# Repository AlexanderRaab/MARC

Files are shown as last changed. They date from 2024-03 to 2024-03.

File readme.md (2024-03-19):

# Project MARC
This repository containes the documentation of the Modular Autonomous Research Companion (MARC).

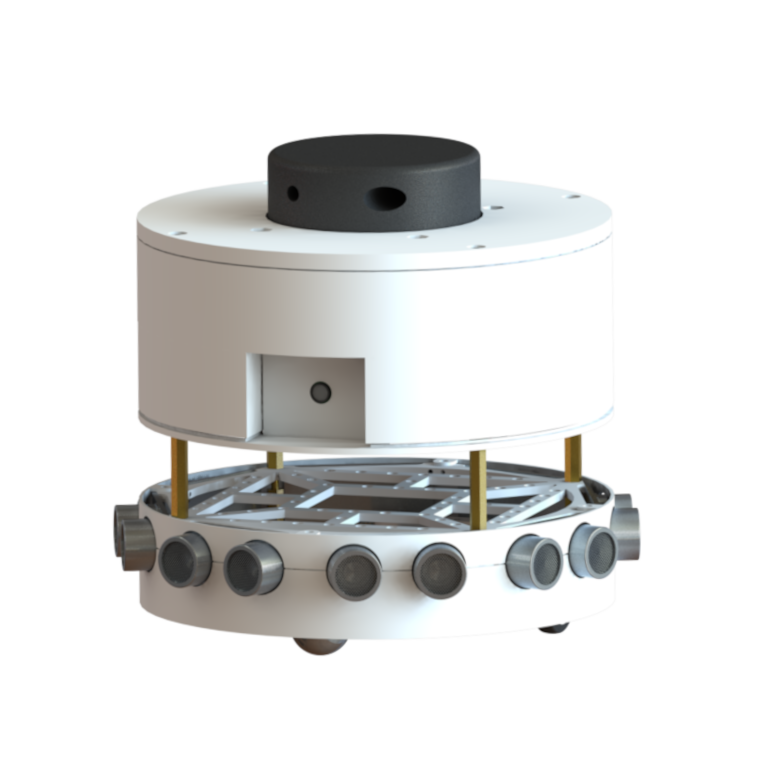
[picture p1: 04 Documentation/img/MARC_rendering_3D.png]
MARC


## Purpose and goal
MARC is a small mobile robot built for at-home testing and experimentation with autonomous robots and all related tasks.
The initial project was started in 2023 with the goal of having a compact and cost-efficient plattform, which can be easily adapted for a multitude of different tasks. For this MARC is setup in different layered modules. Each having a clear functionality as well as providing a defined interface for controlling and for sensory feedback.

## Current status
Up until now, the development mainly focused on setting up the first prototype. Thus, most time was spent on designing a robust implementation of the drive layer, responsible for moving the robot and providing basic sensory feedback for autonomous navigation.

### Hardware
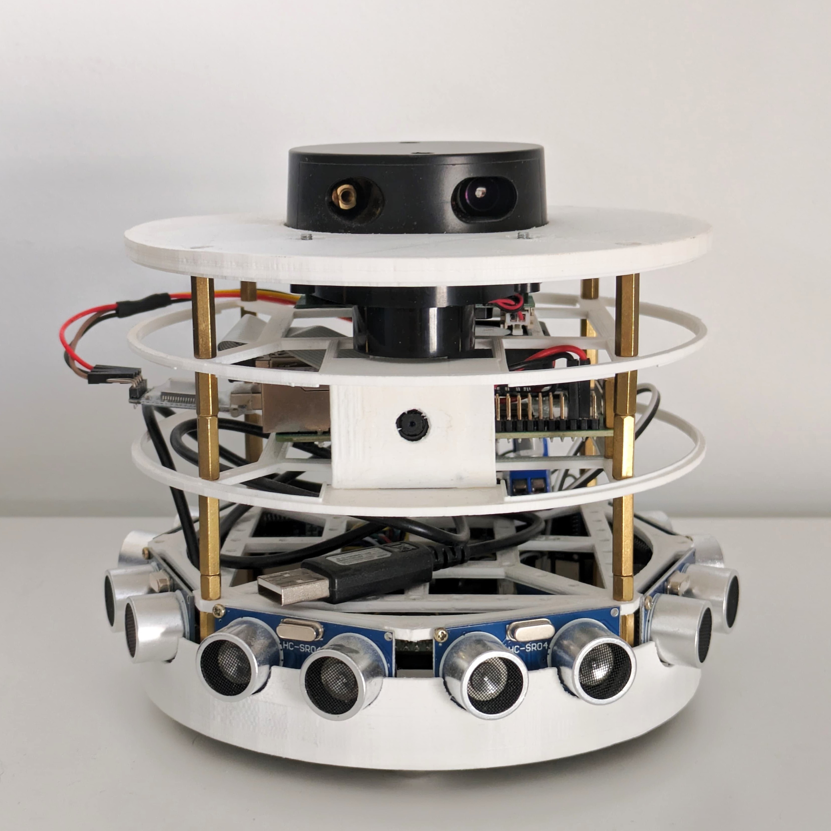
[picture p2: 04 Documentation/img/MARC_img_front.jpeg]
MARC

At this stage, prototypes for the 4 most crucial modules of MARC are completed.

| Module name | Functionality | Interface |
|---|---|---|
| Differential Drive Layer | Locomotion, odometry and basic obstacle detection | micro-ROS via UART |
| Battery Layer | Houses the main battery | n.a. |
| Computation Layer | Containes the main computer and a RGB camera | Joins all other layers |
| LiDAR Layer | Main 2D LiDAR for localization | UART |

#### Differential Drive Layer
This layer is a implementation of a Differential Drive robot. Computations are done on a [Raspberry Pi Pico](https://www.raspberrypi.com/products/raspberry-pi-pico/) mounted on a custom designed PCB. 2 DC motors together with PWM-based motor drivers are used for locomotion. 
The odometry data is currently only computed from wheel encoder signals. Additionally an on-board IMU provides linear acceleration and angular velocity feedback. 
Basic obstacle avoidance can be implemented using 8 ultrasonic distance sensors placed on the circumference of the chassis.

#### Battery Layer
MARC is planned to be powerd either via on-board battery or using a stationary power supply. For now, this layer houses a step-down power supply for converting the input voltage to 12V and 5V in order to supply the other layers.

#### Computation Layer
The main computation unit, a [Raspberry Pi 4B](https://www.raspberrypi.com/products/raspberry-pi-4-model-b/) with 4GB of RAM, is used for all high-level tasks. This includes handling the ROS2 network, processing all data from other layers and providing WIFI connectivity for remote control. Additionally, the main camera is also directly connected to the computer. 

#### LiDAR
For localization, this module contains a 2D LiDAR sensor. The range measurements are streamed over a serial interface and processed directly on the main computer.

### Software
The current version of MARC is based on [ROS2 Humble]( https://docs.ros.org/en/humble/index.html) and [micro-ROS]( https://micro.ros.org/). For now, [Nav2]( https://navigation.ros.org/) is used for all navigation related tasks.

Due to the current focus on hardware prototypes and low-level locomotion control, the ROS2 setup is still under development and may not be completely stable.

Simulation with Gazebo 11          |  Visualization in RVIZ2
:-------------------------:|:-------------------------:
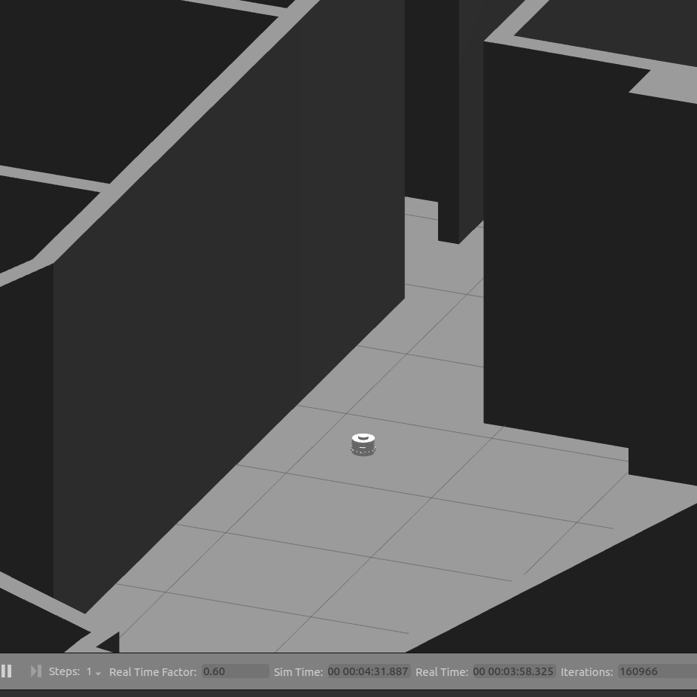
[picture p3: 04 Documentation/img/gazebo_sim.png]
Simulation with Gazebo 11
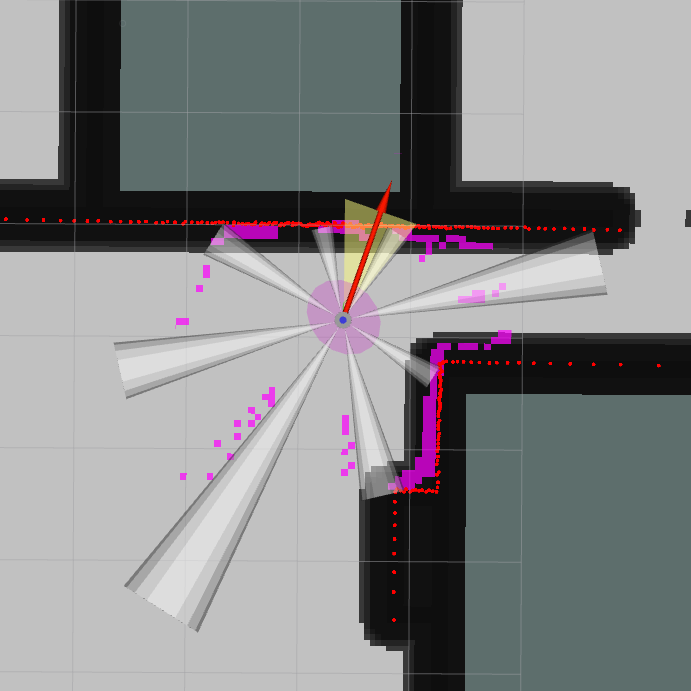
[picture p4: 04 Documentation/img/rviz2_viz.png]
Visualization with RVIZ2
  |  

## Roadmap and planned features

Current development

*   Finishing the intial setup of the ROS2 project for basic SLAM tasks
*   Stabilizing the ROS2 network to improve performance
    *   Revisit the implementation of the camera driver
    *   Improve performance of the custom LiDAR driver
  
Planned features
*   Differential Drive Layer
    *   Implement on-board odometry fusion with an EKF
    *   Change control setup from decoupled PIDs to a model based controller
*   Motion planning and control
    * Implement a trajectory tracking control based on input-output linearization
*   Object detection and classification
    *    Utilize a [YOLO](https://github.com/ultralytics/ultralytics) model for basic on-board detection tasks  
*   Environment interaction
    *   Design and implement a prototype layer for interacting with the environment (e.g. a 3-DOF robotic arm, gripper or fork-lift module)

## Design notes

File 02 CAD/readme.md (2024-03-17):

# CAD
This folder contains all CAD files and assemblies for MARC. Version 1.0 is still in development.

MARC V1.0

## Folder structure
*   Components: 3rd party components for each module
*   Parts: Custom CAD models of individual components
*   Assemblies: Assembled modules
*   Simplified Models: Parts with reduced grade of detail to be used in real-time simulation (includes .stl files)
*   PCBs: Custom PCB files (currently only for the Differential Drive module)

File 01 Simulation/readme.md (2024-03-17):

# Simulation 
This folder contains data and code for simulating parts of the robots software. 

## Data
The _data_ subfolder includes measurement and parameter files for physical components used in the actual robot. Currently only results for the parameter identification of the DC motors can be found there.

## Matlab
Simulations and identification routines can be found in the _Matlab_ folder. 
The following files are currently included:
*   Routines and Matlab code for identifying model parameters of DC motors
    (using an ARX or a 1st order lag element approximation)
*   A SIMULINK model for simulating the Differential Drive kinematics including voltage controlled motors and encoder based odometry

## Example images
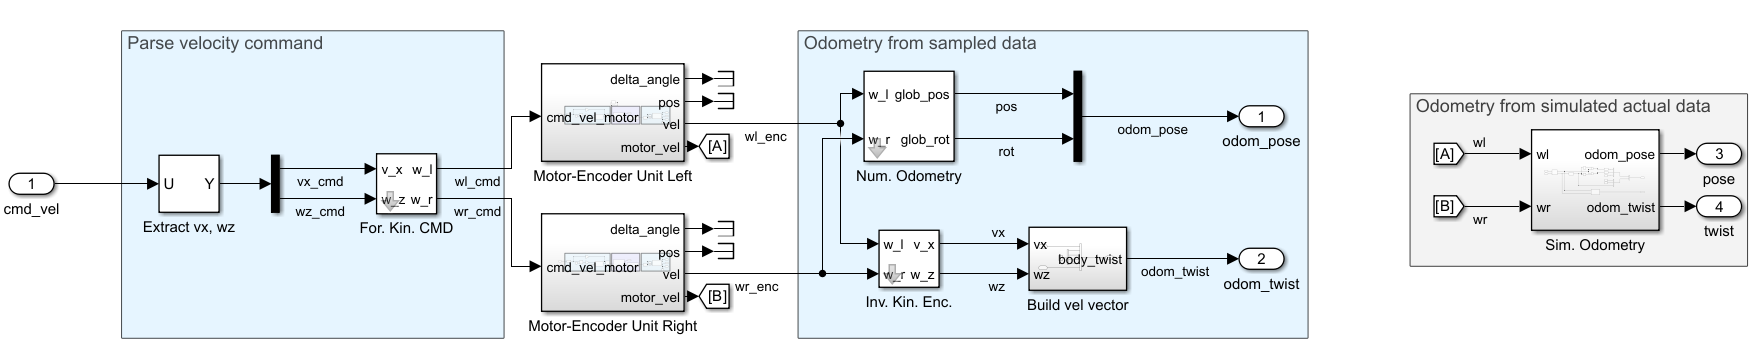
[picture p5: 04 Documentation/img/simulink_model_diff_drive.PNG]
Simulink model


Motor identification ARX model           |  Motor identification PT1 model 
:-------------------------:|:-------------------------:
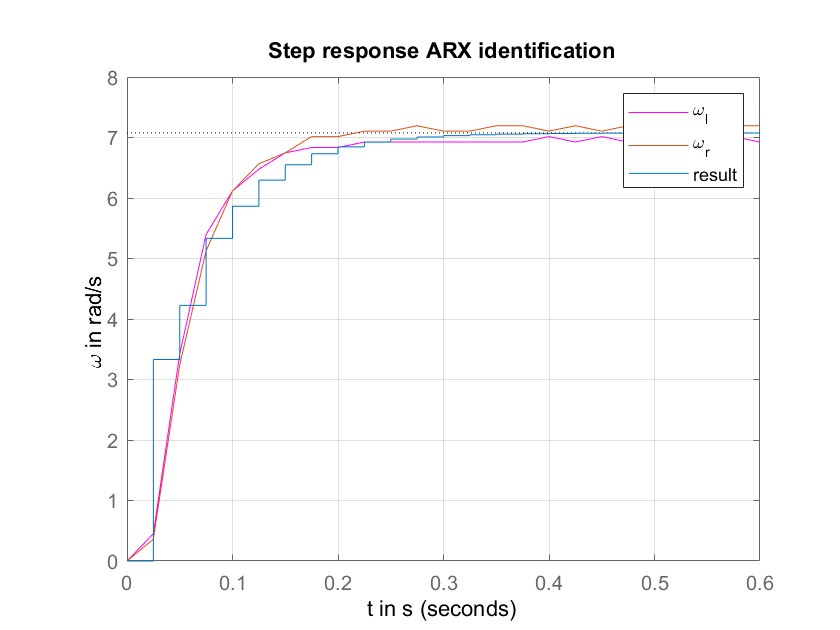
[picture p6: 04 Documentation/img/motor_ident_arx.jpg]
Results ARX identification
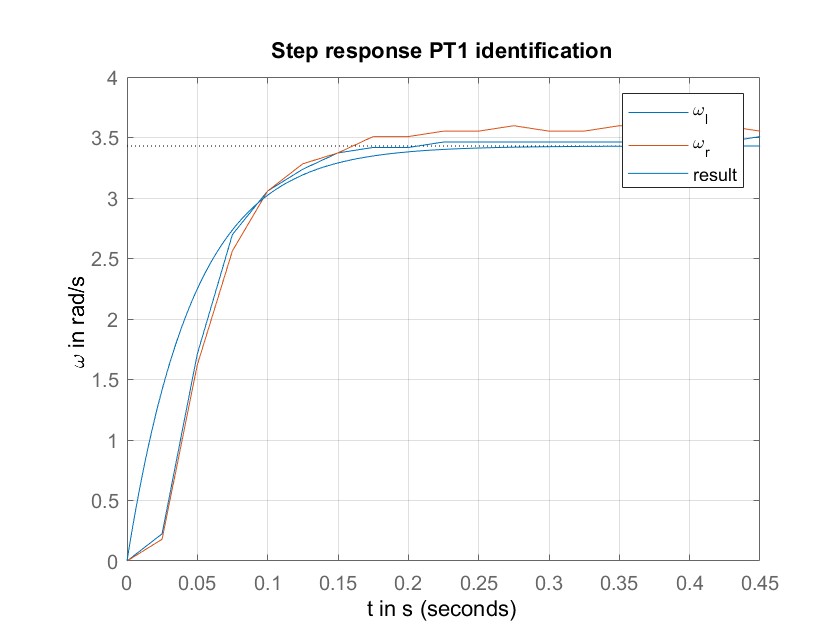
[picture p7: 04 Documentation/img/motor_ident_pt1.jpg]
Results PT1 identification
  |

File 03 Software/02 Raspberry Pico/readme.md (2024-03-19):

# Raspberry Pico
This folder contains code for the Raspberry Pico microcontrollers used to control peripherals of MARC. 

## Pico driver
These directories include the C/C++ code for controlling the Differential Drive module. 

Version 1.0 is only included for completness. Use V1.1, as it includes many stability and performance improvements.

### Setup and tasks
The microcontroller utilizes micro-ROS for integration into the bigger ROS2 project. The implementation is based on timers for executing sampling and control routines. V1.1 fully utilizes both cores of the Raspberry Pico. Core 0 is used for the micro-ROS execution and general sensor sampling including IMU data and ultrasonic range measurements. Core 2 is solely used for kinematic transformations of velocity commands, decoupled DC motor control via PWM and calculation of the wheel odometry.

The implementation is mainly done header-only to stay independet of the hardware platform.

The code project includes the following files:
*   [diff_drive_utils.h](pico_driver_v1.1/diff_drive_utils.h): Methods and calculations Differential Drive kinematics
*   [driver_config.h](pico_driver_v1.1/driver_config.h): Parameter configuration of the driver including dimensions, ROS2 config and control settings
*   [pico_driver.c](pico_driver_v1.1/pico_driver.c): Main project file
*   [pico_interface.h](pico_driver_v1.1/pico_interface.h): Methods for interacting with the Raspberry Pico including reading and writing I/O signals and accessing timers
*   [quadrature_encoder.pio](pico_driver_v1.1/quadrature_encoder.pio): Register-based quadrature encoder reading [source](https://github.com/raspberrypi/pico-examples/blob/master/pio/quadrature_encoder/quadrature_encoder.pio)
*   [ros_interface.h](pico_driver_v1.1/ros_interface.h): Methods for interacting with the ROS2 network e.g. publishing and listening to topics

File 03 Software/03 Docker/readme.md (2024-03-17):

# Docker
This directory includes all files for running the ROS2 project inside a Docker container.

**Attention: The docker environment is still under development and may not work as intended!**
**The implementation is currently only tested for Windows 10 and requires [vcxsrv](https://uni-tuebingen.de/en/fakultaeten/wirtschafts-und-sozialwissenschaftliche-fakultaet/faecher/fachbereich-wirtschaftswissenschaft/wirtschaftswissenschaft/fb-wiwi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)**

## Usage
Paste all custom ROS2 packages to [ros2_ws/src](ros2_ws/src).

On Windows, build the docker container with

    ./build_docker.ps1

Use 

    ./run_docker.ps1

to run the container and

    ./attach_docker.ps1

to open new shell windows.

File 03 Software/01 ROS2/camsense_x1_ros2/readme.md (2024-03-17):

# CAMSENSE_X1_ROS2
This packag is a custom C++ driver and ROS2 wrapper for using the _Camsense X1_ LiDAR.

Credit goes to [Vidicon](https://github.com/Vidicon/camsense-X1) for providing detailed information about the protocol used by the sensor.

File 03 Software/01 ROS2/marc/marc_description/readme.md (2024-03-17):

# MARC_DESRIPTION
This package includes all URDF models of components for MARC.

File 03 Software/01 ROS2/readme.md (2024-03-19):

# ROS2 
This folder contains all custom ROS2 packages. 
**Note: MARC is currently developed for ROS2 Humble**

## Usage
For detailed descriptions of how to run the ROS2 project, check the [marc_bringup](marc/marc_bringup) package.

For launching the default simulation use

    ros2 launch marc_bringup MARC.launch.py simulation:=True

after building an sourcing the workspace.

Use 

    ros2 launch marc_bringup MARC.launch.py simulation:=False

for launching the project on the physical robot.

## Dependencies
The ROS2 project depends on
*   General
    *   [xacro](https://index.ros.org/p/xacro/)  
    *   [rviz2](https://index.ros.org/p/rviz2/)
    *   [robot_localization](https://index.ros.org/p/robot_localization/)
    *   [navigation2](https://navigation.ros.org/)
    *   [robot_state_publisher](https://index.ros.org/p/robot_state_publisher/)
    *   [joint_state_publisher](https://index.ros.org/p/joint_state_publisher/)
*   Simulation only
    *   [gazebo_ros](https://index.ros.org/p/gazebo_ros/)
    *   [gazebo_ros_pkgs](https://index.ros.org/p/gazebo_ros_pkgs/)
*   Physical robot
    *   [micro_ros_agent](https://github.com/micro-ROS/)
    *   [image_tools](https://index.ros.org/p/image_tools/)

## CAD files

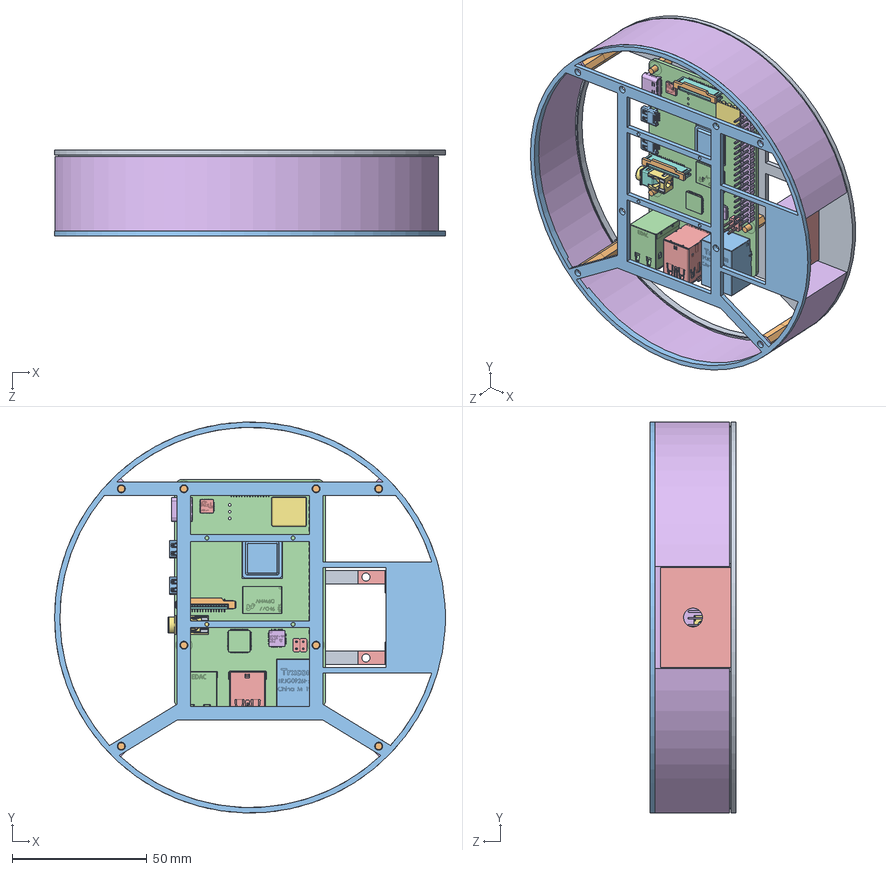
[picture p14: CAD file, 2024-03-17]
02 CAD/V1.0/03 Assemblies/1.02.00 Raspberry Pi 4B Layer.SLDASM
145.0 x 145.0 x 32.0 mm
1.02.01 Raspberry Pi 4B Lower Plate
Spacer M3 x 12
1.02.02 Raspberry Pi 4B Upper Plate
1.0 Plate raspberry Pi 4_1
2.0. PIN HEADER one_1
3.0 PIN HEADER 20_1
4.0 metal plate._1
2.2 part 2 with combine x 2
1.1 part 1 metal pin x 2
3.3 plastic x 2
5.0 CPU Broadcom_1
6.0 9FD77 D9WHV_1
7.0 MxL_1
8.0 Gigabit Ethernet Transceiver_1
9.0 VLI PCIe USB 3.0 Controller_1
card slot part 2 metal pin
sd card slot v1
part 3 v1
11.0 Female micro HDMI connector_1 x 2
15.0 2x USB 2.0 PORT_1
14.0 2x USB 3.0 PORT_1
10.0 Female USB connector_1
part 4 microphone plug
Microphone plug part 1
part 2 microphon plug metal
part 3 microphone plug
12.0 Gigabit ethernet port raspberry
9.0 VLI PCIe USB 3.0 Controller v1_1
1.02.03 Camera Holder
1.02.04 Raspberry Layer Cover

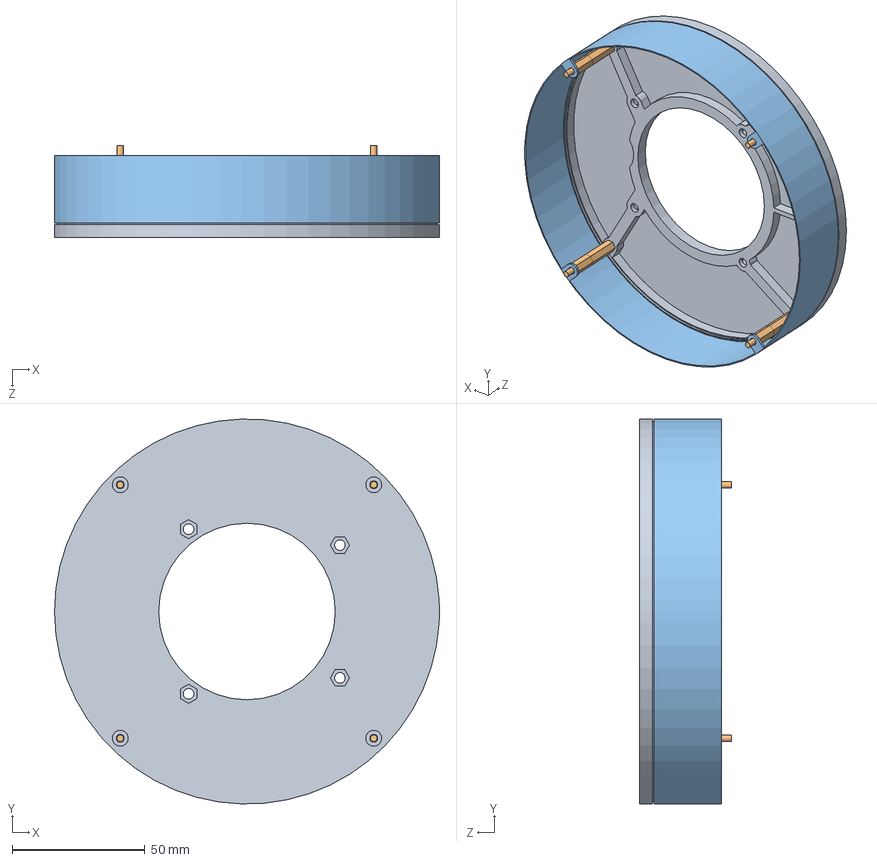
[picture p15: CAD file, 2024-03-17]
02 CAD/V1.0/03 Assemblies/1.03.00 Lidar Layer.SLDASM
145.0 x 144.9 x 34.8 mm
1.03.01 Camsense X1 Plate
Spacer M3 x 8
1.03.02 Camsense X1 Cover

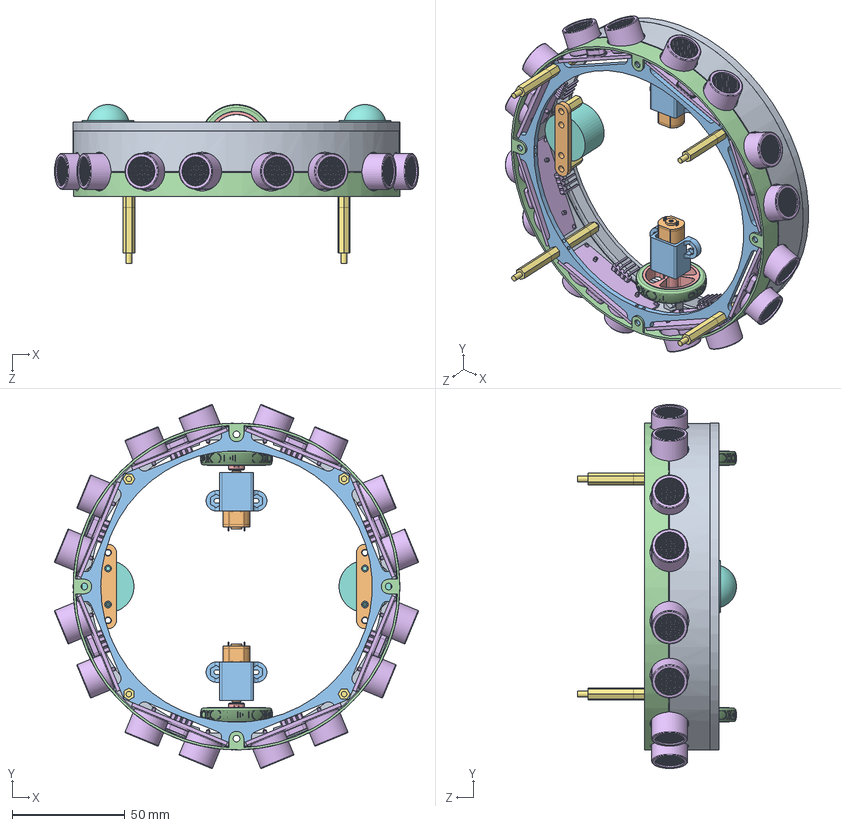
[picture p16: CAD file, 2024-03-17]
02 CAD/V1.0/03 Assemblies/1.01.00 Differential Drive Platform.SLDASM
161.5 x 161.5 x 70.6 mm
1.01.01 Base Layer
Micro Metal Gear Motor x 2
Motor Bracket x 2
Pololu-Wheel-32x7mm-tire x 2
Pololu-Wheel-32x7mm-rim x 2
HC-SR04 x 8
Spacer M3 x 20
Ball Bracer 3_4 x 2
1.01.02 Base Layer Lower Cover
1.01.03 Ball Castor Clip x 2
1.01.04 Ultrasonic Sensor Fixation
1.01.05 Base Layer Upper Cover

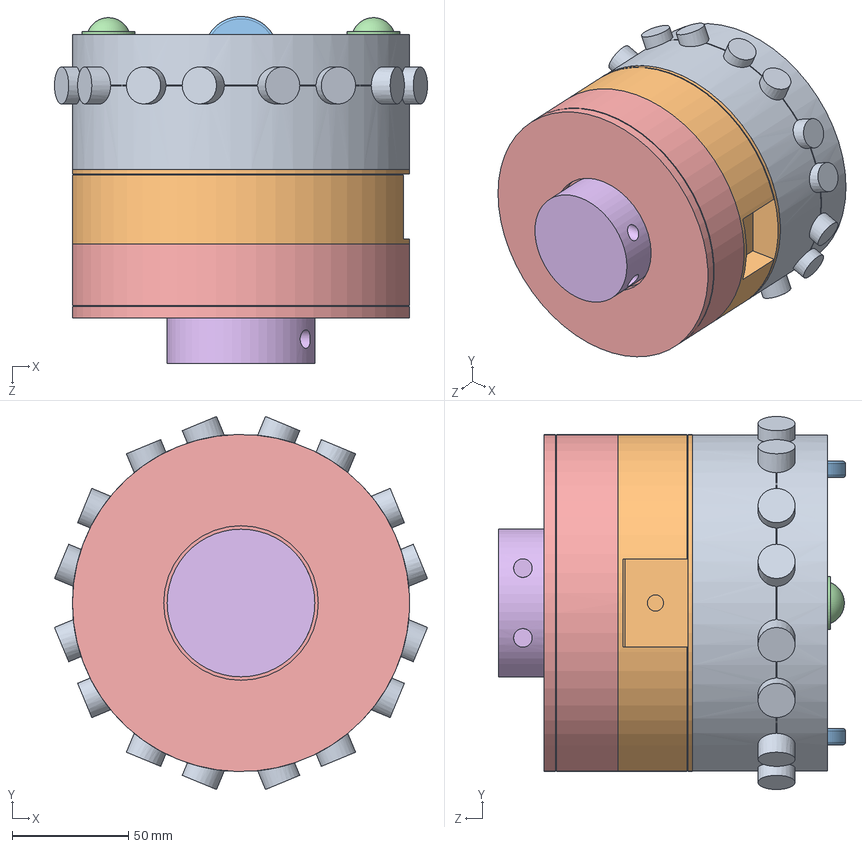
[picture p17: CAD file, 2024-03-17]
02 CAD/V1.0/04 Simplified Models/1.01 MARC Simplified.SLDASM
160.5 x 160.5 x 149.2 mm
1.01 Differntial Drive Plattform Simplified
1.03 Raspberry Pi 4B Layer Simplified
0.01 Wheel 32x7mm x 2
0.02 Ball Castor 075 Inch x 2
1.04 Camsense X1 Layer Simplified
0.03 Camsense X1

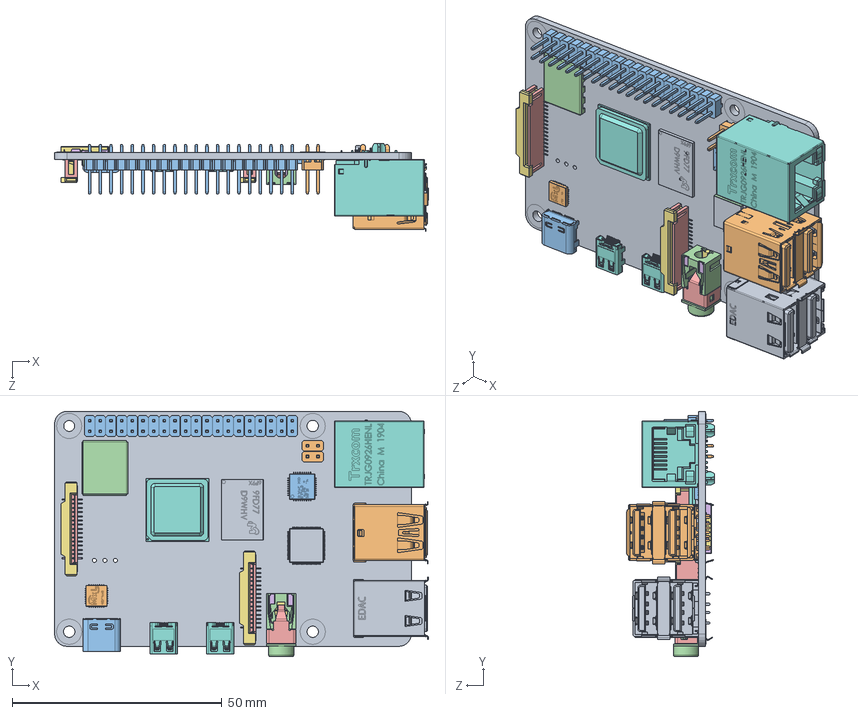
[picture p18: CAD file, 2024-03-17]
02 CAD/V1.0/01 Components/raspberry-pi-4-model-b-5.snapshot.9/Raspberry Pi 4 Model B.SLDASM
89.1 x 58.5 x 20.8 mm
1.0 Plate raspberry Pi 4_1
2.0. PIN HEADER one_1
3.0 PIN HEADER 20_1
4.0 metal plate._1
2.2 part 2 with combine x 2
1.1 part 1 metal pin x 2
3.3 plastic x 2
5.0 CPU Broadcom_1
6.0 9FD77 D9WHV_1
7.0 MxL_1
8.0 Gigabit Ethernet Transceiver_1
9.0 VLI PCIe USB 3.0 Controller_1
card slot part 2 metal pin
sd card slot v1
part 3 v1
11.0 Female micro HDMI connector_1 x 2
15.0 2x USB 2.0 PORT_1
14.0 2x USB 3.0 PORT_1
10.0 Female USB connector_1
part 4 microphone plug
Microphone plug part 1
part 2 microphon plug metal
part 3 microphone plug
12.0 Gigabit ethernet port raspberry
9.0 VLI PCIe USB 3.0 Controller v1_1

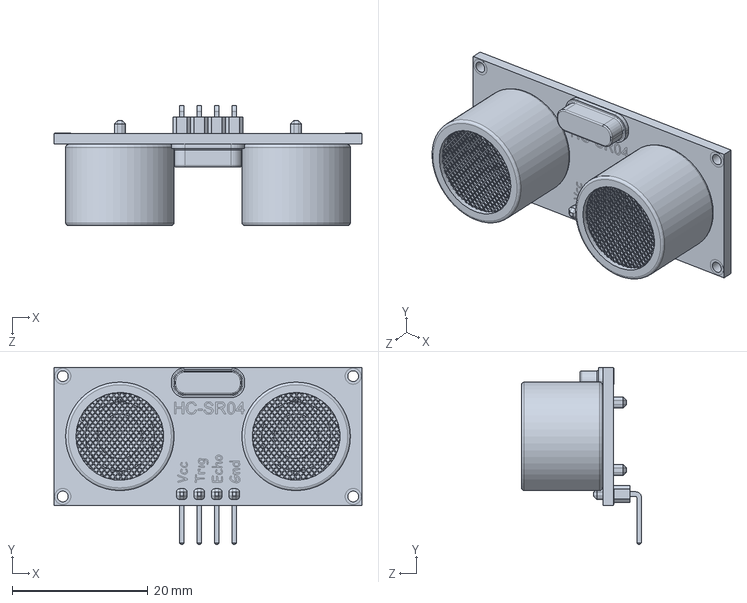
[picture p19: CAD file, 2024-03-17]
02 CAD/V1.0/01 Components/HC-SR04.sldprt
45.4 x 26.1 x 17.7 mm

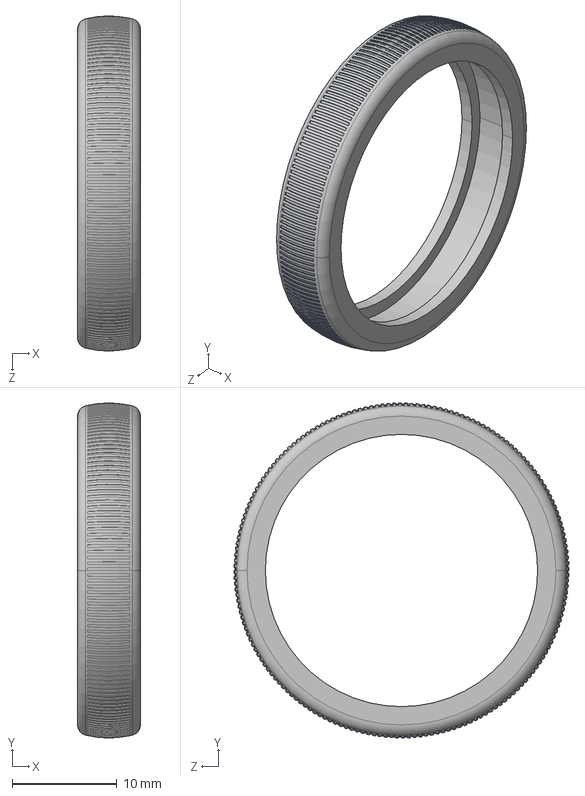
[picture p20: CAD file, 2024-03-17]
02 CAD/V1.0/01 Components/Pololu Wheel 32x7mm/Pololu-Wheel-32x7mm-tire.STEP
6.00 x 32.0 x 32.0 mm

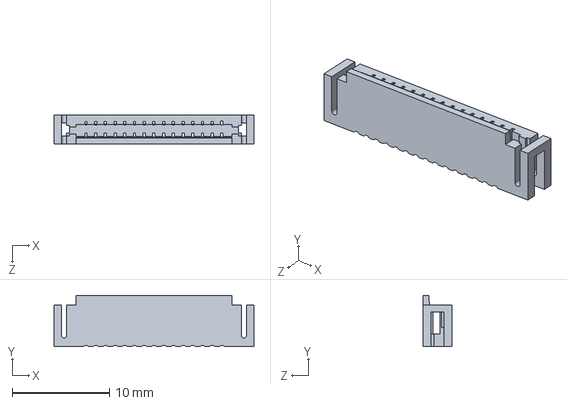
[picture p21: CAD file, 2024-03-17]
02 CAD/V1.0/01 Components/raspberry-pi-4-model-b-5.snapshot.9/1. display connector assembly/2.2 part 2 with combine.SLDPRT
20.6 x 5.30 x 3.00 mm

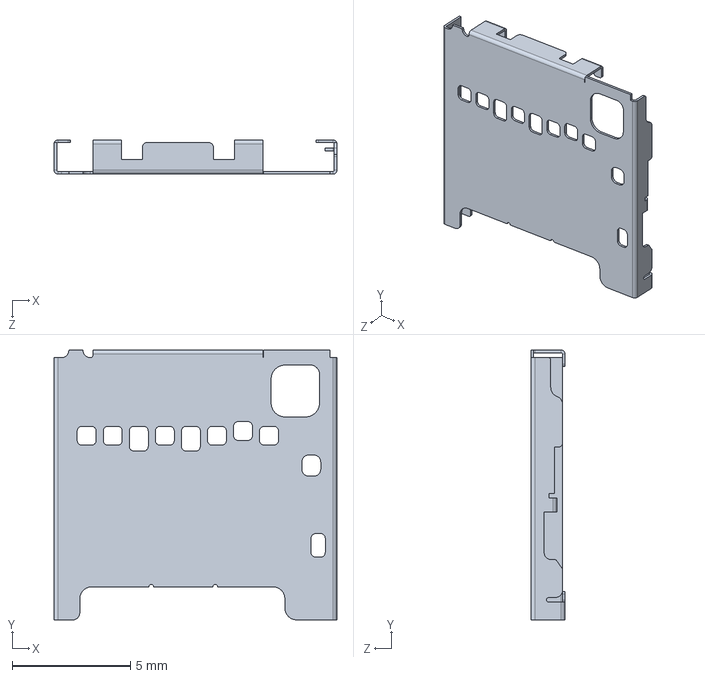
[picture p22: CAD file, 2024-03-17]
02 CAD/V1.0/01 Components/raspberry-pi-4-model-b-5.snapshot.9/2. card slot/part 3 v1.SLDPRT
11.9 x 11.4 x 1.45 mm

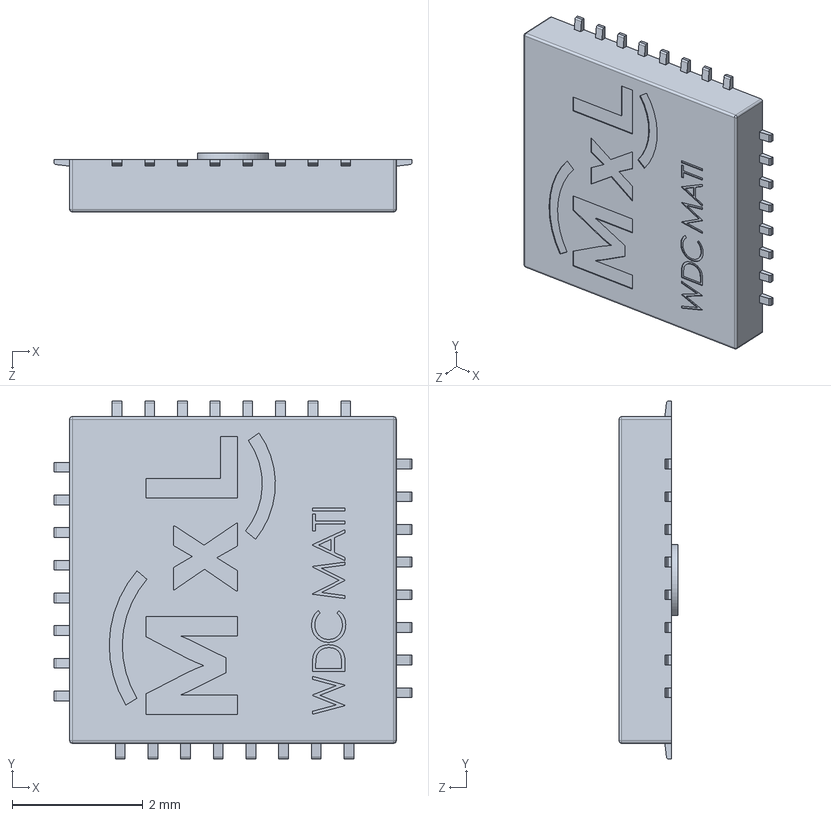
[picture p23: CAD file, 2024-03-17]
02 CAD/V1.0/01 Components/raspberry-pi-4-model-b-5.snapshot.9/7.0 MxL.SLDPRT
5.48 x 5.48 x 0.9 mm

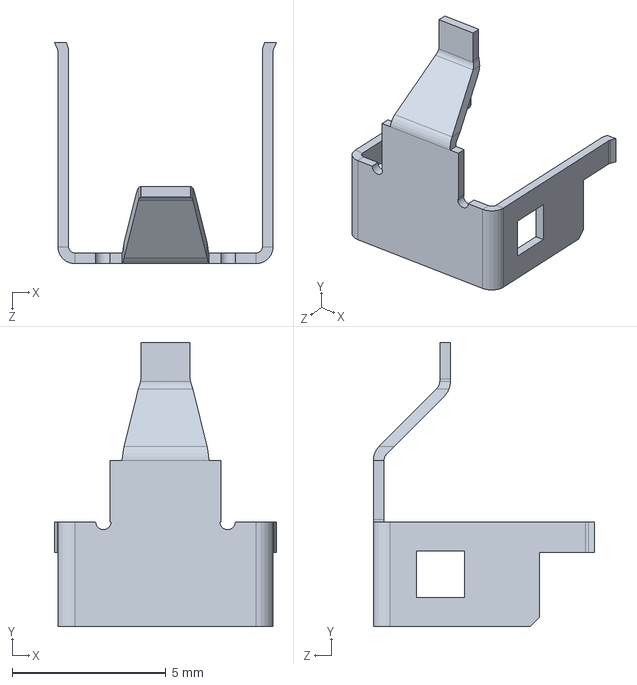
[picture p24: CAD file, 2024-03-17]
02 CAD/V1.0/01 Components/raspberry-pi-4-model-b-5.snapshot.9/Microphone plug/Microphone plug part 1.SLDPRT
7.23 x 9.23 x 7.20 mm

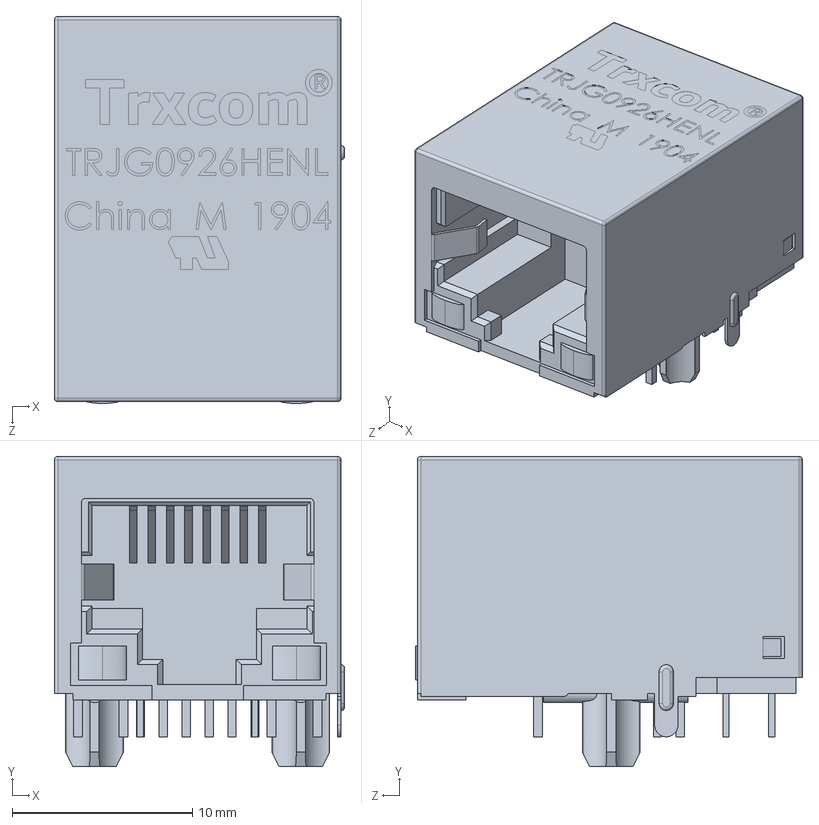
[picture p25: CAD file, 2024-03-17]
02 CAD/V1.0/01 Components/raspberry-pi-4-model-b-5.snapshot.9/Microphone plug/part/12.0 Gigabit ethernet port raspberry.SLDPRT
16.1 x 17.2 x 21.4 mm

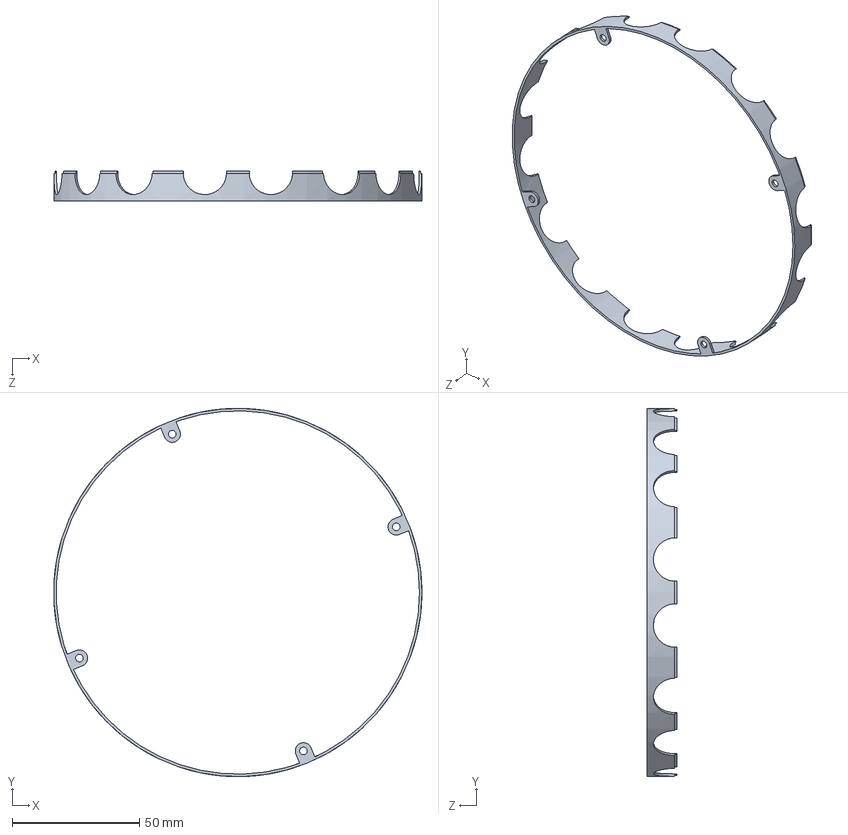
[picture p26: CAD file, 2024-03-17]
02 CAD/V1.0/02 Parts/1.01.05 Base Layer Upper Cover.SLDPRT
144.9 x 144.9 x 11.6 mm

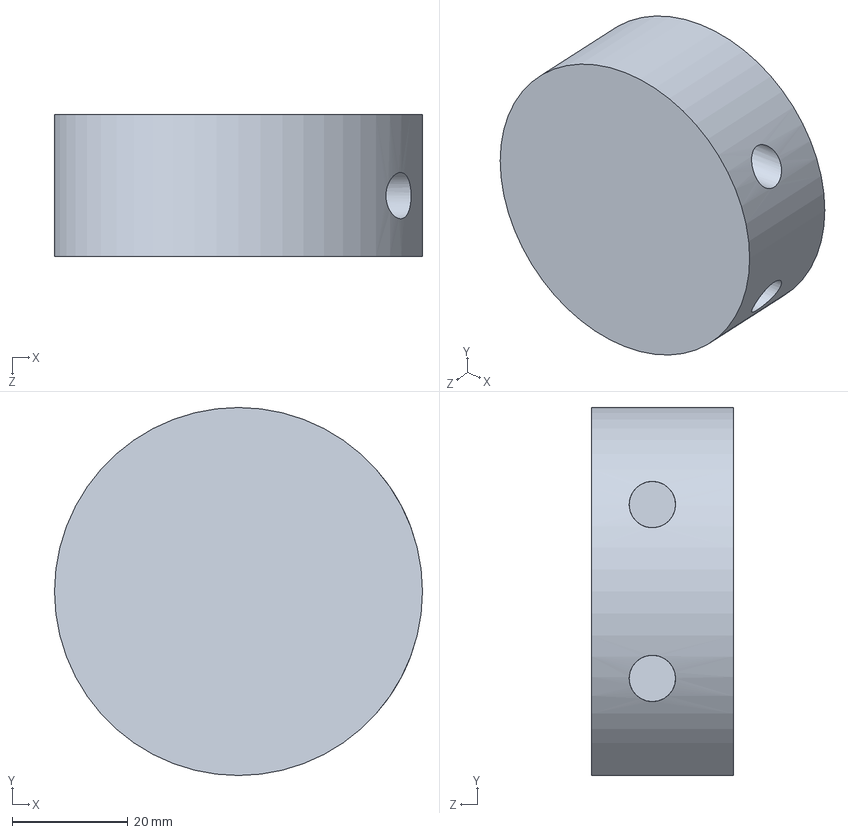
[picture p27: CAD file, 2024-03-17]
02 CAD/V1.0/04 Simplified Models/0.03 Camsense X1.SLDPRT
63.5 x 63.5 x 24.5 mm

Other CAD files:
02 CAD/V1.0/01 Components/raspberry-pi-4-model-b-5.snapshot.9/Display connector assembly_2.sldasm
02 CAD/V1.0/01 Components/raspberry-pi-4-model-b-5.snapshot.9/Display connector assembly.sldasm
02 CAD/V1.0/01 Components/raspberry-pi-4-model-b-5.snapshot.9/Microphone plug assembly.sldasm
02 CAD/V1.0/01 Components/raspberry-pi-4-model-b-5.snapshot.9/Card slot assembly.sldasm
02 CAD/V1.0/01 Components/Ball Bracer 3_4.SLDPRT
02 CAD/V1.0/01 Components/Camsense_X1.SLDPRT
02 CAD/V1.0/01 Components/Camsense_X1_Lidar.SLDPRT
02 CAD/V1.0/01 Components/Micro Metal Gear Motor.SLDPRT
02 CAD/V1.0/01 Components/Motor Bracket.SLDPRT
02 CAD/V1.0/01 Components/Pololu Wheel 32x7mm/Pololu-Wheel-32x7mm - Pololu-Wheel-32x7mm-rim-1.STL
02 CAD/V1.0/01 Components/Pololu Wheel 32x7mm/Pololu-Wheel-32x7mm - Pololu-Wheel-32x7mm-tire-2.STL
02 CAD/V1.0/01 Components/Pololu Wheel 32x7mm/Pololu-Wheel-32x7mm-rim.IGS
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

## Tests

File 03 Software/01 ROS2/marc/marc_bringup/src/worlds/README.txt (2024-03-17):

Gazebo .world file mt_og5.world currently contains absolute path to model file for user "pi" and workspace "dev_ws".
For other user names adjust line 148 and 169 to fit new path.

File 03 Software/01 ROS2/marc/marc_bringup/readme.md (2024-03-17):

# MARC_BRINGUP
This package is used to configure and launch the whole ROS2 project for simulating or running the physical MARC in different configurations.

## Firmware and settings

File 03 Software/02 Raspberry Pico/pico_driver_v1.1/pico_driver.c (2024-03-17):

/* microROS Differantial Driver Robot
    Author:     Alexander Raab
    E-Mail:     alex.raab@liwest.at
    Date:       17.06.2023
    Version:    1.2
    Licence:    TODO

    An application for the Raspberry Pi Pico to work as a ROS2-driver for a differential drive robot.

    TODO: Additional sensors, tf2 publisher odom -> base_link (optional), parameters for relevant variables, 
    optimize for higher sample rates
        
*/


#include <stdio.h>
#include <math.h>

#include <rcl/rcl.h>
#include <rcl/error_handling.h>
#include <rclc/rclc.h>
#include <rclc/executor.h>

#include <rmw_microros/rmw_microros.h>

#include "driver_config.h"
#include "diff_drive_utils.h"
#include "pico_interface.h"
#include "ros_interface.h"

// Shutsdown the node
void shutdown_node()
{
    RCCHECK(rcl_subscription_fini(&cmd_vel_sub, &node_driver));
	RCCHECK(rcl_publisher_fini(&odom_pub, &node_driver));
    RCCHECK(rcl_publisher_fini(&imu_pub, &node_driver));
	RCCHECK(rcl_node_fini(&node_driver));
}

int main()
{
    // Setup transport system for RPi Pico
    rmw_uros_set_custom_transport(
		true,
		NULL,
		pico_serial_transport_open,
		pico_serial_transport_close,
		pico_serial_transport_write,
		pico_serial_transport_read
	);

    // Initilize Pico GPIO etc.
    pico_setup();

    // Initialize controller parameters
    PID_update_parameters(driver.motor_left->velocity_controller);
    PID_update_parameters(driver.motor_right->velocity_controller);

    allocator = rcl_get_default_allocator();

    // Wait for agent successful ping for 2 minutes.
    const int timeout_ms = 1000; 
    const uint8_t attempts = 120;
    RCCHECK(rmw_uros_ping_agent(timeout_ms, attempts));

    // Init support
    rcl_init_options_t init_options = rcl_get_zero_initialized_init_options();
    RCCHECK(rcl_init_options_init(&init_options, allocator));
    RCCHECK(rcl_init_options_set_domain_id(&init_options, DOMAIN_ID));
    RCCHECK(rclc_support_init_with_options(&support, 0, NULL, &init_options, &allocator));

    // Node
    RCCHECK(rclc_node_init_default(&node_driver, "driver_node", NAMESPACE_DRIVER, &support));

    // Setup node functionalities
    setup_publishers();
    setup_subscribers();
    setup_timers();
    setup_msg();

    // Executor
    RCCHECK(rclc_executor_init(&executor, &support.context, CONTEXT_CNT, &allocator));
    RCCHECK(rclc_executor_add_timer(&executor, &timer_sample));
    RCCHECK(rclc_executor_add_subscription(&executor, &cmd_vel_sub, &msg_cmd_vel, &cmd_vel_callback, ON_NEW_DATA));

    // Loop
    gpio_put(PIN_MOT_ON, 1);

    rcl_ret_t ret = RCL_RET_OK; 
    while (ret == RCL_RET_OK)
    {   
        // Perform non-critical tasks 
        if(timer_update_sample)
        {
            update_sonar();
            timer_update_sample = false;
        }
        rclc_executor_spin_some(&executor, RCL_MS_TO_NS(1));
    }
        
    //rclc_executor_spin(&executor);
    gpio_put(PIN_MOT_ON, 0);

    shutdown_node();

    return 0;
}

// Main loop on core 1 - used for velocity control
void core1_main()
{
    repeating_timer_t ctrl_timer;
    add_repeating_timer_ms(TIMER_CONTROL_INTERVAL, timer_ctrl_callback, NULL, &ctrl_timer);

    while(1)
    {   
        if(timer_update_ctrl)
        {

            // Store current velcoity command for use on core 1
            mutex_enter_blocking(&mtx_cmd_vel);
            set_target_vel_body();
            mutex_exit(&mtx_cmd_vel); 

            // Read data from PIO and update measurement data
            mutex_enter_blocking(&mtx_odom_data);
            update_odometry_data(quadrature_encoder_get_count(pio_enc_L, PIO_ENC_L_SM), -quadrature_encoder_get_count(pio_enc_R, PIO_ENC_R_SM));
            mutex_exit(&mtx_odom_data);

            // Apply velocity control
            control_velocity();      
            set_motor_pwm(pwm_out_mot[0], pwm_out_mot[1]);  
             
            timer_update_ctrl = false;
        }
    }

    cancel_repeating_timer(&ctrl_timer);
}

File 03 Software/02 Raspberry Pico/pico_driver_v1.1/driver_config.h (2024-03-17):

/*  Includes all configuration settings for the differential drive plattform.
    Author:     Alexander Raab
    E-Mail:     alex.raab@liwest.at
    Date:       17.06.2023
    Version:    1.1
    Licence:    TODO

    This header is used to store all configuaration settings, global variables and macros relevant for the differential drive plattform in one file.
*/

#pragma once

// ROS2 settings
// --- Main settings
#define DOMAIN_ID (0)
#define NAMESPACE_DRIVER ""                         // Node namespace 
#define NAMESPACE_SENSOR ""                         // Namespace for sensor data

// --- Frames
#define BASE_LINK "base_link"                       // Robot base link
#define IMU_FRAME "imu"                             // IMU sensor link
#define ODOM_FRAME "odom"                           // Odometry link
#define ULTRASONIC_1_FRAME "ultrasonic_1_link"      // Ultrasonic sensor 1 link
#define ULTRASONIC_2_FRAME "ultrasonic_2_link"      // Ultrasonic sensor 2 link
#define ULTRASONIC_3_FRAME "ultrasonic_3_link"      // Ultrasonic sensor 3 link
#define ULTRASONIC_4_FRAME "ultrasonic_4_link"      // Ultrasonic sensor 4 link
#define ULTRASONIC_5_FRAME "ultrasonic_5_link"      // Ultrasonic sensor 5 link
#define ULTRASONIC_6_FRAME "ultrasonic_6_link"      // Ultrasonic sensor 6 link
#define ULTRASONIC_7_FRAME "ultrasonic_7_link"      // Ultrasonic sensor 7 link
#define ULTRASONIC_8_FRAME "ultrasonic_8_link"      // Ultrasonic sensor 8 link

// --- Topics
#define IMU_TOPIC "imu"                             // IMU data topic
#define ODOM_TOPIC "odom"                           // Odometry data topic
#define SONAR_TOPIC "ultrasonic/range"              // Ultrasonic range data topic
#define CMD_VEL_TOPIC "/cmd_vel"                    // Veclocity command topic

// Misc.
#define CONTEXT_CNT (3)                             // Context count - must match number of timers and subscribers

// Robot settings
// --- Hardware specifications
#define ENCODER_CPR         (12.)                   // Pulses per revoultion of motor shaft
#define GEAR_RATIO          (75.)                   // Gear ratio x:1
#define WHEEL_CPR           (900.)                  // Pulses per revoultion of wheel
#define WHEEL_RADIUS        (0.016)                 // Radius of a wheel
#define WHEEL_TRACK         (0.0625)                // Distance from center of the robot to one wheel

#define SONAR_FOV           (0.2618)                // Measurement angle of the HC-SR04 in radians (15°)
#define SONAR_MIN_RANGE     (0.002)                 // Shortes measureable distance of the HC-SR04
#define SONAR_MAX_RANGE     (4.000)                 // Farthest measureable distance of the HC-SR04

// --- Sample and controller settings
// --- --- Sensors enable
#define ULTRASONIC_5_ON     (true)                  // Enable ultrasonic sensor 5
#define ULTRASONIC_8_ON     (true)                  // Enable ultrasonic sensor 8

// --- --- Timers
#define TIMER_SAMPLE_INTERVAL   (50)                // Publisher and sensor sample timer in ms
#define TIMER_CONTROL_INTERVAL  (25)                // Control timer in ms

// --- --- Motor velocity control
#define MAX_MOT_PWM         (65025)                 // Maximum PWM value for motor control
#define MIN_MOT_PWM         (5500)                  // Minimum PWM value for motor control
#define MAX_WHEEL_VEL_ANG   (50.)                   // Maximum angular wheel velocity in rad/s
#define MIN_WHEEL_VEL_ANG   (0.625)                 // Minimum angular wheel velocity in rad/s

#define MOT_PID_P           (.25)                   // Motor PID controller P-gain
#define MOT_PID_I           (7.0)                   // Motor PID controller I-gain
#define MOT_PID_D           (.01)                   // Motor PID controller D-gain
#define MOT_PID_N           (50.)                   // Motor PID controller filter coefficient
#define MOT_CTR_FF          (1300.5)                // Motor control feed-forward constant MAX_MOT_PWM/MAX_WHEEL_VEL_ANG




// Raspberry Pico
// --- Hardware config
// --- --- GPIO Pins
#define PIN_I2C0_SDA    (0)                         // I2C SDA
#define PIN_I2C0_SCL    (1)                         // I2C SCL
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

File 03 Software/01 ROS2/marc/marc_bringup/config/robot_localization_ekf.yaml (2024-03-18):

ekf_node_odom:
    ros__parameters:
        use_sim_time: true
        frequency: 20.0
        sensor_timeout: 0.5
        two_d_mode: true
        transform_time_offset: 0.0
        transform_timeout: 0.0
        # print_diagnostics: true
        debug: false
        # debug_out_file: /path/to/debug/file.txt
        publish_tf: true
        publish_acceleration: false
        reset_on_time_jump: true

        map_frame: map
        odom_frame: odom
        base_link_frame: base_link
        world_frame: odom

        odom0: /odom
        odom0_config: [true, true, false,     # x, y, z
                       false, false, true,    # r, p, y
                       true,  false,  false,  # vx, vy, vz
                       false, false, true,    # wx, wy, wz
                       false, false, false]   # ax, ay, az
        # odom0_queue_size: 2
        # odom0_nodelay: false
        odom0_differential: false
        odom0_relative: false
        # odom0_pose_rejection_threshold: 5.0
        # odom0_twist_rejection_threshold: 1.0

        imu0: /imu
        imu0_config: [false, false, false,
                      true,  true,  true,
                      false, false, false,
                      true,  true,  true,
                      false,  false,  false]
        
        # imu0_nodelay: false
        imu0_differential: false
        imu0_relative: true
        # imu0_queue_size: 7
        # imu0_pose_rejection_threshold: 0.8                
        # imu0_twist_rejection_threshold: 0.8               
        # imu0_linear_acceleration_rejection_threshold: 0.8 
        imu0_remove_gravitational_acceleration: true
        
        twist0: /cmd_vel
        use_control: true
        # stamped_control: false
        control_timeout: 0.2
        control_config: [true, false, false, false, false, true]
        acceleration_limits: [2., 0.0, 0.0, 0.0, 0.0, 6.28]
        deceleration_limits: [2., 0.0, 0.0, 0.0, 0.0, 10.]
        #acceleration_gains: [0.8, 0.0, 0.0, 0.0, 0.0, 0.9]
        #deceleration_gains: [1.0, 0.0, 0.0, 0.0, 0.0, 1.0]

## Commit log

2024-03-17 Updated main readme
    [CamsenseX1.urdf.xacro, DiffDriveBase.stl, HC-SR04.urdf.xacro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]
2024-03-17 Added simulation readme
    [Parts.xlsx]
2024-03-17 Added documentation for ROS2 project
    [CamsenseX1.urdf.xacro, HC-SR04.urdf.xacro, LSM6DS33.urdf.xacro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]
2024-03-18 Added initial nav2 config
    [base.urdf.xacro, robot_localization_ekf.yaml, wheel.urdf.xacro]
